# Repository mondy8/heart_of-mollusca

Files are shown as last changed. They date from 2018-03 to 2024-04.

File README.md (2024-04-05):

# Heart of Mollusca

+ [Heart of Mollusca 紹介動画](https://vimeo.com/240353748)
+ [ADAA アジアデジタルアートアワード 学生インタラクティブアート部門 優秀賞](https://adaa.jp/ja/winners/winners2017.html)
+ [北九州デジタルクリエイターコンテスト2018 入選](https://kdcc.info/archive/2018.html)
+ [ADADA2016 Art paper](https://github.com/ImaokaHiroaki/heart_of-mollusca/blob/master/paper/art_paper.pdf)

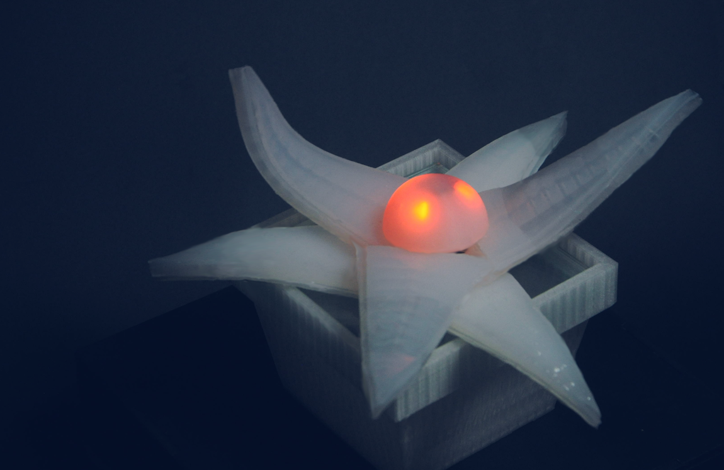
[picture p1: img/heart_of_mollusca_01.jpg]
写真1

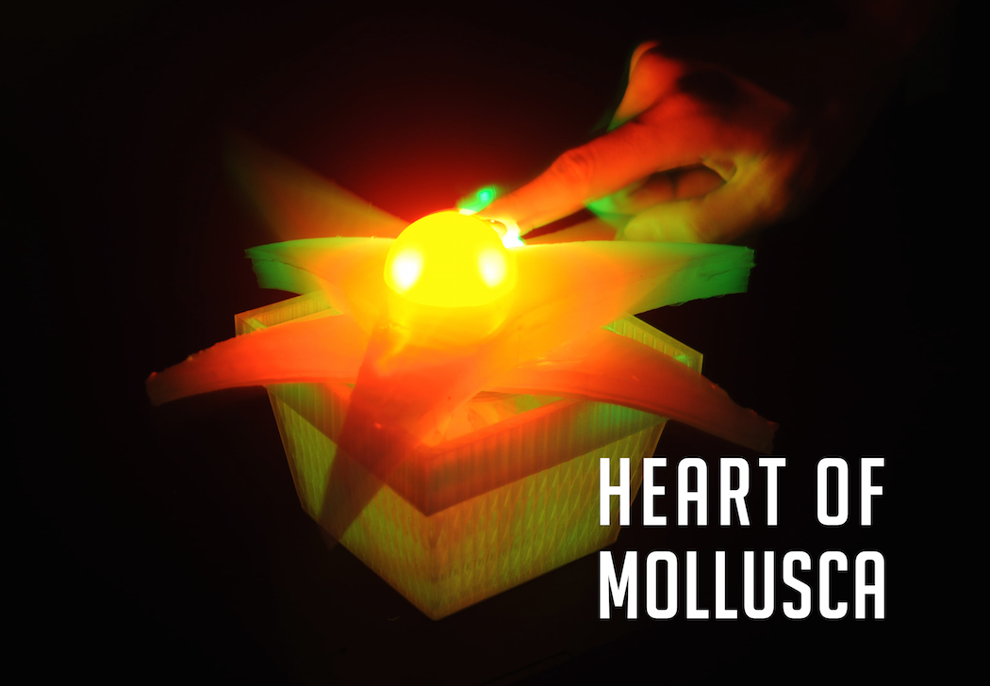
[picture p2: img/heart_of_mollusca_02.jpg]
写真2

 
 従来のロボットのイメージには「機械的」というキーワードが常に存在していた。ロボットは重厚であり、硬く、冷たいといったイメージである。それゆえに、ロボットには心がない、人間とロボットがコミュニケーションをとることはできない、といった意見が現状では多く見られる。昨今登場したソフトロボティクスという分野は、柔らかいロボットを研究する分野である。ソフトロボティクスを専攻している研究者たちは、「柔らかさ」をテーマにしたロボットを制作することで、何か今までになかったロボットの新しい可能性を探求している。本作品では、従来のロボットのイメージとは異なる有機的な表現を取り入れたロボットを制作することで、今までになかった新たなロボットとのコミュニケーションを実現したいと考えている。

 「Heart of Mollusca」は、人間の心拍とともに動くソフトロボットである。このロボットは、何もしていない状態だと動かず、人の心拍を検知した時、その人の心拍に合わせた動きを始める。鑑賞者はまず、作品の触手の部分にあるパルスセンサーを触る。すると「Heart of Mollusca」の中心部はゆっくりと赤く光りはじめる。そのあと、心拍と共に触手の部分が呼吸をするように膨張・収縮を繰り返す。人差し指で触手を触っているため、心拍にあわせた触手の膨張を感じることができる。「Heart of Mollusca」は、シリコンを使って中から空気を入れることによって動かしている。このシリコンによる柔らかさを用いた軟体動物のような動きは、鑑賞者に独特な感覚をもたらす。
 
 「Heart of Mollusca」を体験した鑑賞者たちは、今まで持っていた従来のロボットとのイメージとの差から興味・関心を抱く人や、ロボットの外見から想像していなかった動きに驚き、生理的な嫌悪感を抱く人など、様々な反応の違いを見せた。有機的な表現を取り入れたことに関しては、心拍とロボットの動きを連動したことにより、ロボットから生命らしさを感じると答えた人が多かった。心拍との連動を取り入れたことに関しては、普段意識することのない自分の心拍を視覚と触覚により体験することで、興味深く感じた人を多く見受けることができた。「Heart of Mollusca」を体験した人たちからは従来のロボットとの触れ合いとは異なった反応が多く得ることができた。

## レシピ

1. シリコン
	+ Ecoflex [(サツク株式会社)](https://vimeo.com/240353748)
	+ DragonSkin [(サツク株式会社)](https://vimeo.com/240353748)
	+ SilPoxy [(サツク株式会社)](https://vimeo.com/240353748)
2. 電気系統
	+ Arduino UNO [(スイッチサイエンス)](https://www.switch-science.com/catalog/789/)
	+ ACアダプター *2 [(robotshop)](https://www.robotshop.com/jp/ja/sfe-power-supply-9vdc-650ma.html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)
	+ Arduino用USBケーブル[(robotshop)](https://www.robotshop.com/jp/ja/usb-cable-a-b-arduino.html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)
	+ ソレノイド電磁石バルブ [(amazon)](https://www.amazon.co.jp/uxcell-a14010700ux0271-uxcell-%E3%82%BD%E3%83%AC%E3%83%8E%E3%82%A4%E3%83%89%E9%9B%BB%E7%A3%81%E7%9F%B3%E5%BC%81-%E3%82%BD%E3%83%AC%E3%83%8E%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)
	+ 気圧センサー MIS-2500-015G [(秋月)](http://akizukidenshi.com/catalog/g/gP-07272/)
	+ 心拍センサー [(スイッチサイエンス)](https://www.switch-science.com/catalog/1135/)
	+ Mitsumi マイクロエアポンプ [(amazon)](https://www.amazon.co.jp/Mitsumi-R-14-%E3%83%9E%E3%82%A4%E3%82%AF%E3%83%AD%E3%82%A8%E3%82%A2%E3%83%9D%E3%83%B3%E3%83%97-200mA-%E3%83%9F%E3%83%8B%E3%83%9D%E3%83%B3%E3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)
	+ 2Aデュアルモーターコントローラー [(秋月)](http://akizukidenshi.com/catalog/g/gM-06680/)
3. 小物系
	+ シリコンチューブ 4mm x 6mm [(モノタロウ)](https://www.monotaro.com/g/00250063/)
	+ シリコンチューブコネクター (二方型・クロス型・T型) [(モノタロウ)](https://www.monotaro.com/p/8933/4497/)
	+ PP ディスクカップ [(モノタロウ)](https://www.monotaro.com/p/5843/8712/?t.q=%83%7E%83L%83V%83%93%83O%83J%83b%83v)
	+ 極薄ニトリルゴム手袋 [(モノタロウ)](https://www.monotaro.com/g/00277898/?t.q=%8E%E8%91%DC)
	+ アルミ丸パイプ [(モノタロウ)](https://www.monotaro.com/g/00280306/)
	+ テルモシリンジ [(モノタロウ)](https://www.monotaro.com/p/0292/1861/?t.q=%83V%83%8A%83%93%83W)
	+ 割り箸
	+ 計量器
	
4. 設備
	+ 真空チャンバー
	+ オーブン
	+ 3Dプリンター
	+ CNCミリングマシン（基板切削用）
	
## Arduino配線図

instruction 説明

## 3Dデータ素材

* 球体上部分
* 球体下部分
* Ecoflex用フタ部分
* Ecoflex用土台
* DragonSkin用土台

instruction 説明

## Eagle切削基板

instruction 説明

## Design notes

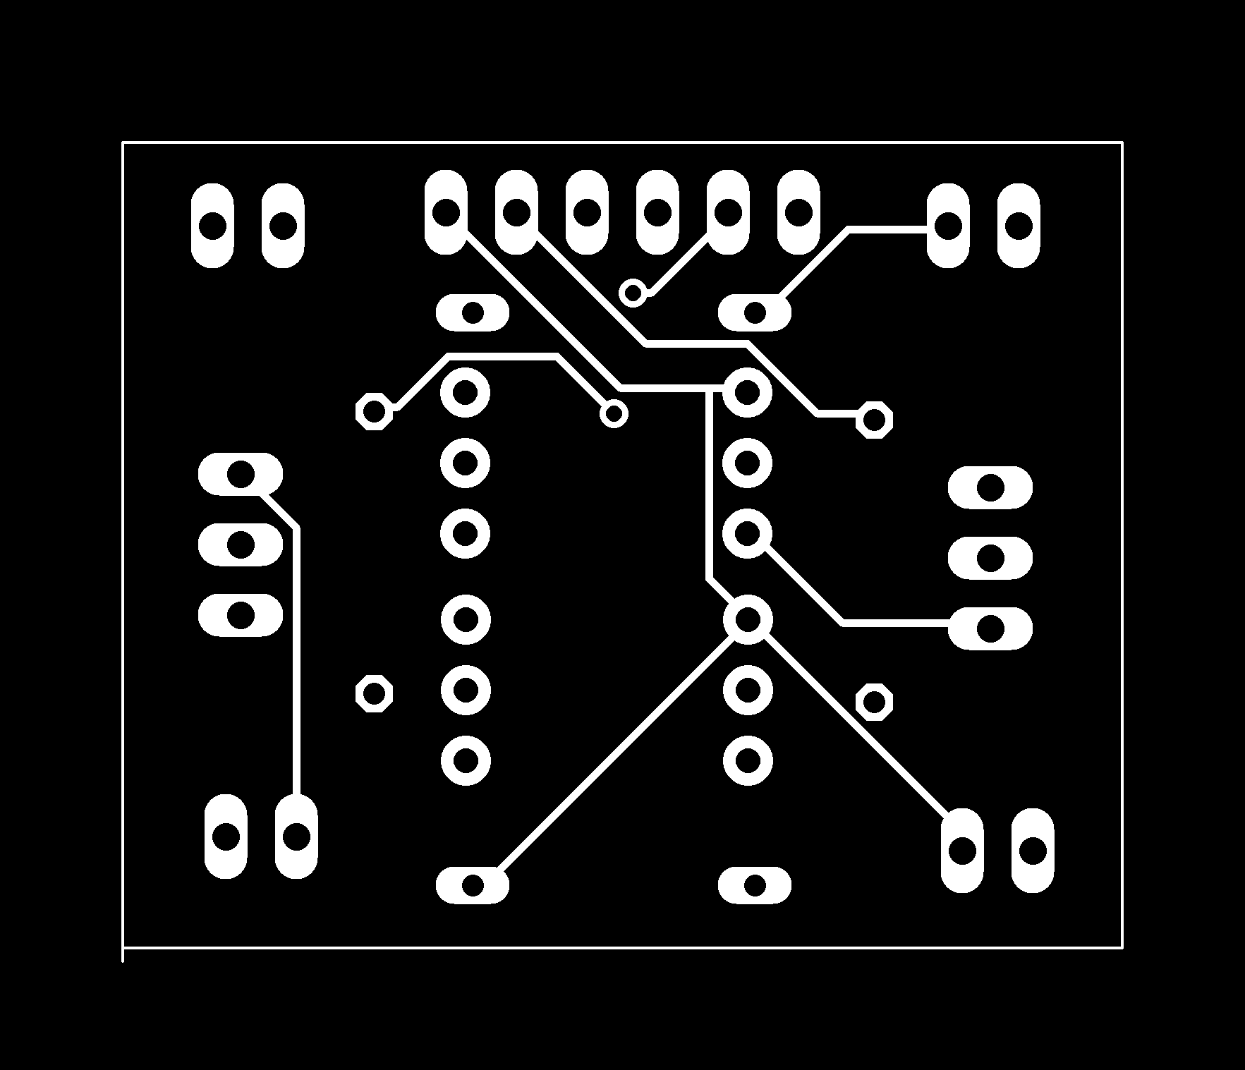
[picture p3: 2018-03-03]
Eagle/img/ura.png

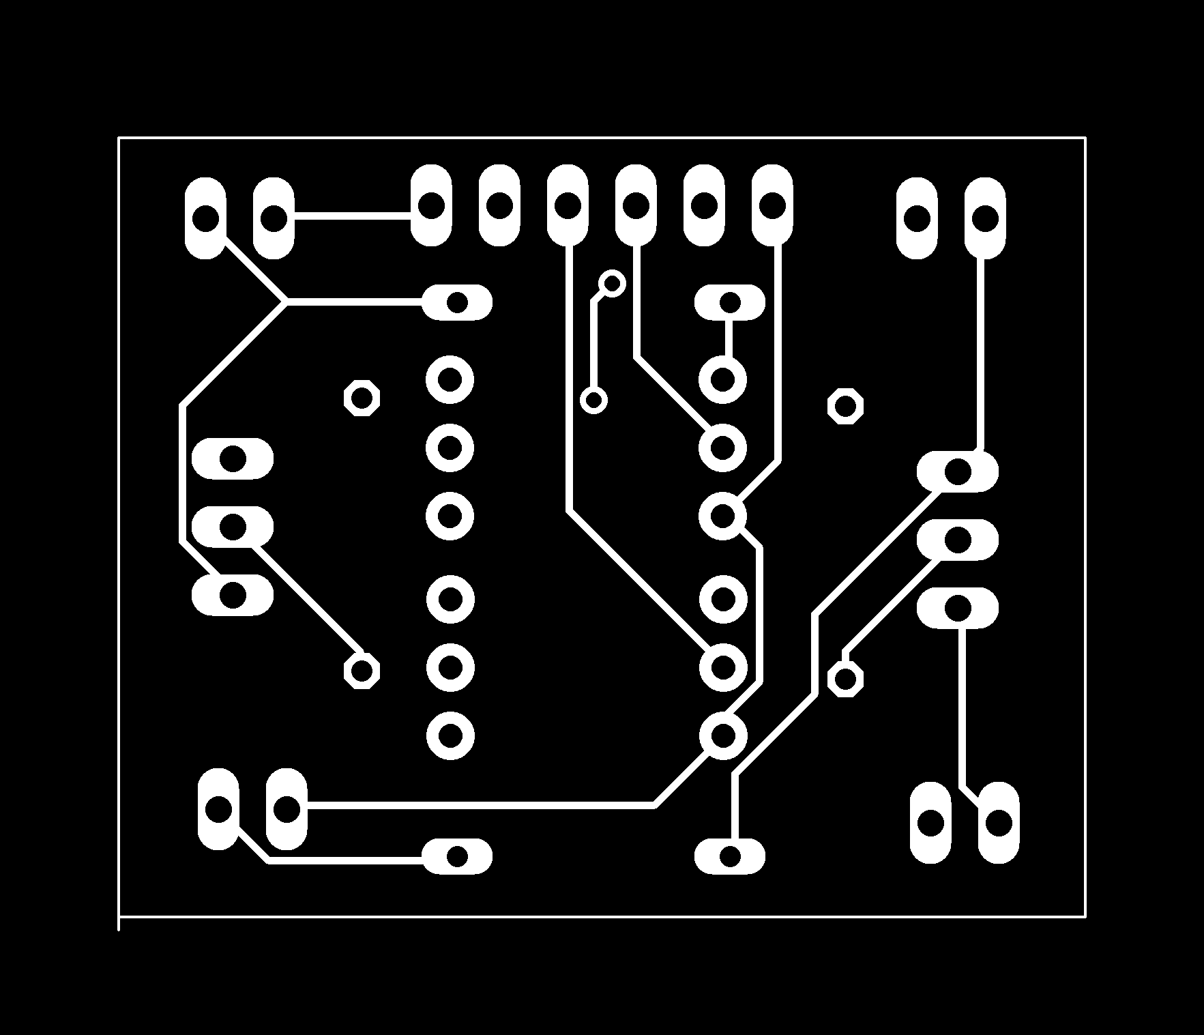
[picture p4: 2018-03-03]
Eagle/img/omote.png

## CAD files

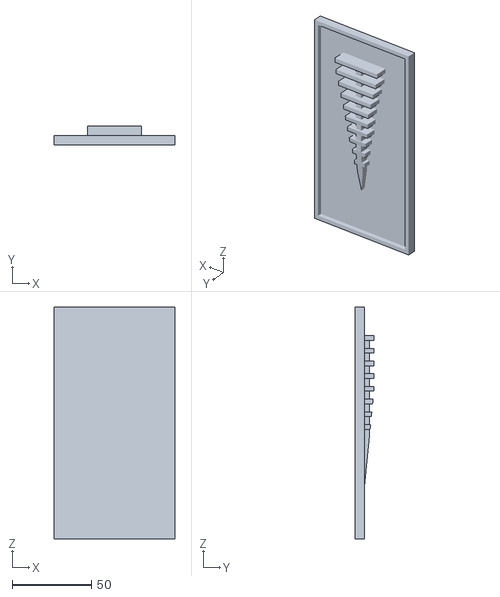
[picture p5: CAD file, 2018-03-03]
3D-data/mold_eco_shita.stl
76.0 x 12.0 x 146.0

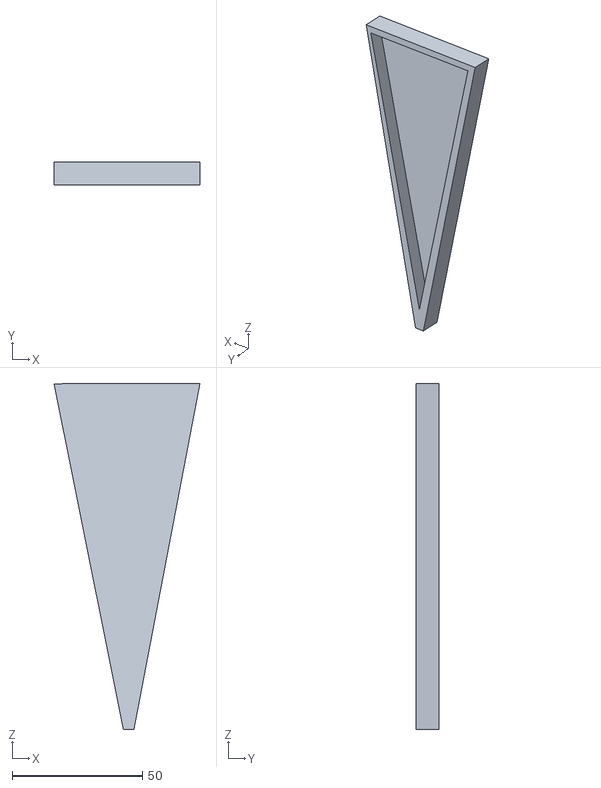
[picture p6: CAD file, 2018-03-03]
3D-data/mold_dragonskin.stl
56.1 x 9.00 x 133.0

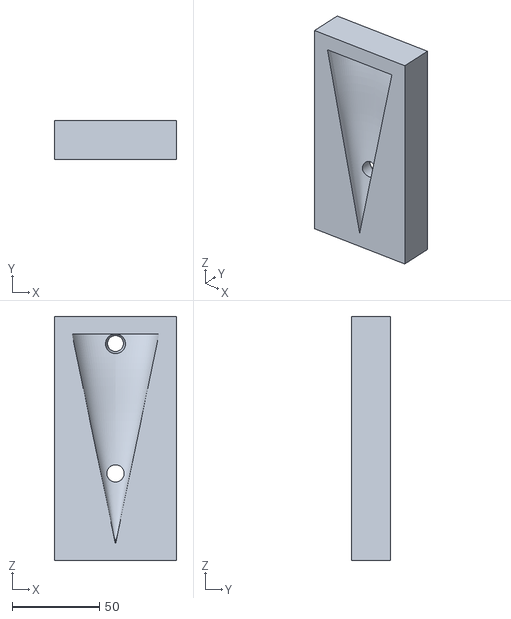
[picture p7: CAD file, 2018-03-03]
3D-data/mold_eco_futa.stl
70.0 x 22.5 x 140.0

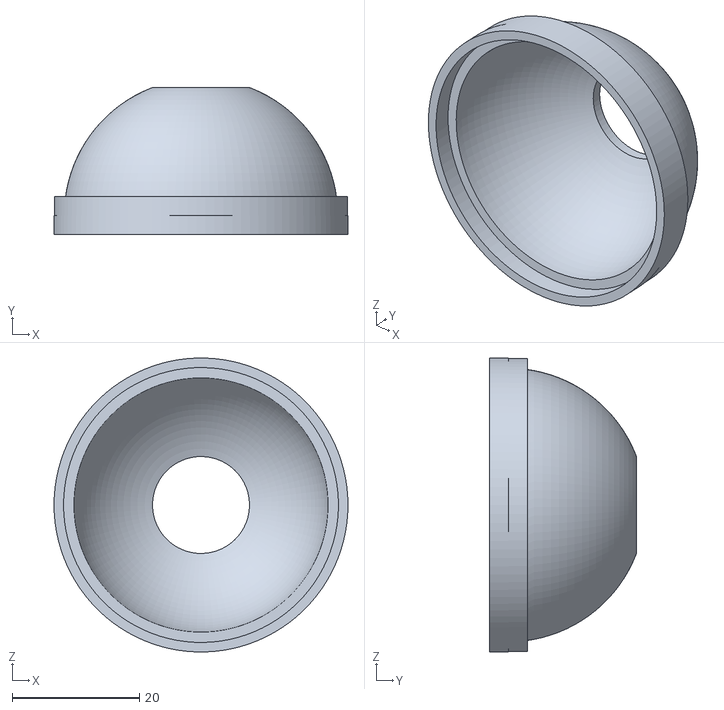
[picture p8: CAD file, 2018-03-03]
3D-data/circle_futa.stl
46.2 x 23.1 x 46.2

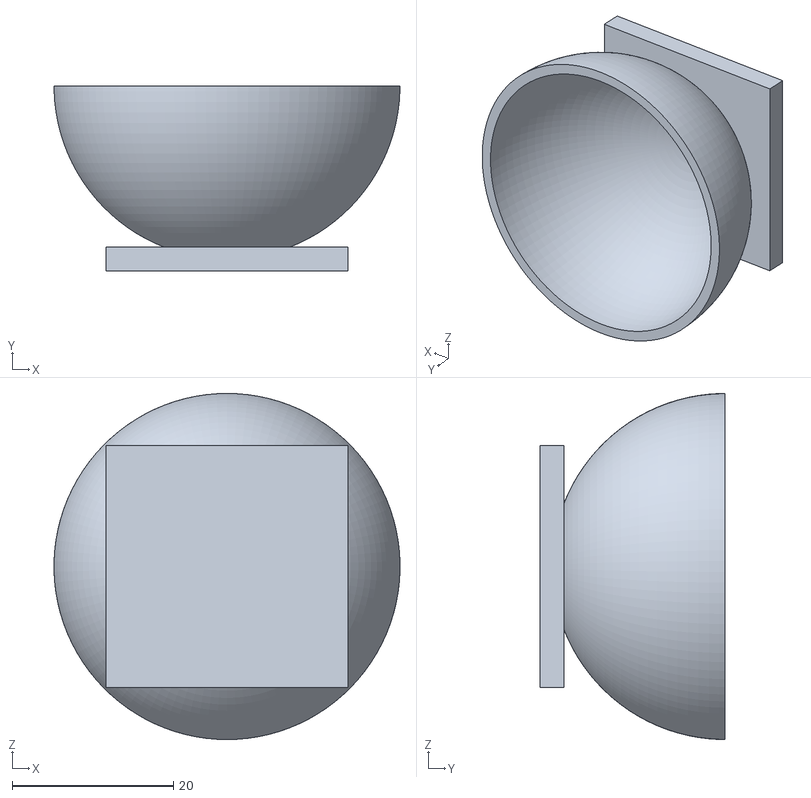
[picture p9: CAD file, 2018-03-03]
3D-data/circle_shita.stl
43.0 x 23.0 x 43.0

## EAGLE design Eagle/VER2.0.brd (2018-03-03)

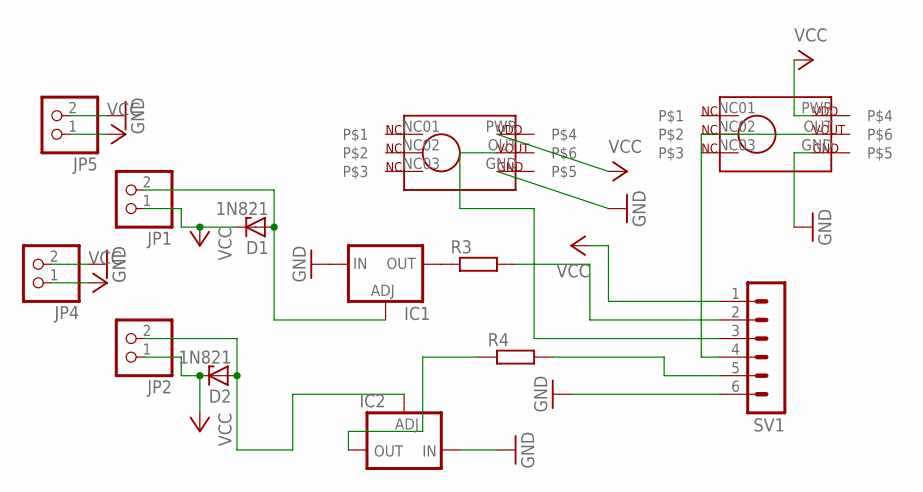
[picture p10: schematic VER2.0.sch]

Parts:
D1, D2: 1N821; DO35Z10
IC1, IC2: LM317TS; 317TS
JP1, JP2, JP4, JP5: PINHD-1X2; 1X02
R3, R4: R-EU_0207/10; 0207/10
SV1: MA06-1
U$1, U$2: MIS-2500

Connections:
GND: IC1.3 (IN), IC2.3 (IN), JP4.2, JP5.2, SV1.6, U$1.GND, U$2.GND
unnamed: R3.2, SV1.2
unnamed: SV1.3, U$1.OUT
unnamed: IC2.2 (OUT), R4.1
unnamed: D2.A, IC2.1 (ADJ), JP2.2
unnamed: IC1.2 (OUT), R3.1
unnamed: D1.A, IC1.1 (ADJ), JP1.2
unnamed: SV1.4, U$2.OUT
unnamed: R4.2, SV1.5
VCC: D1.C, D2.C, JP1.1, JP2.1, JP4.1, JP5.1, SV1.1, U$1.PWR, U$2.PWR

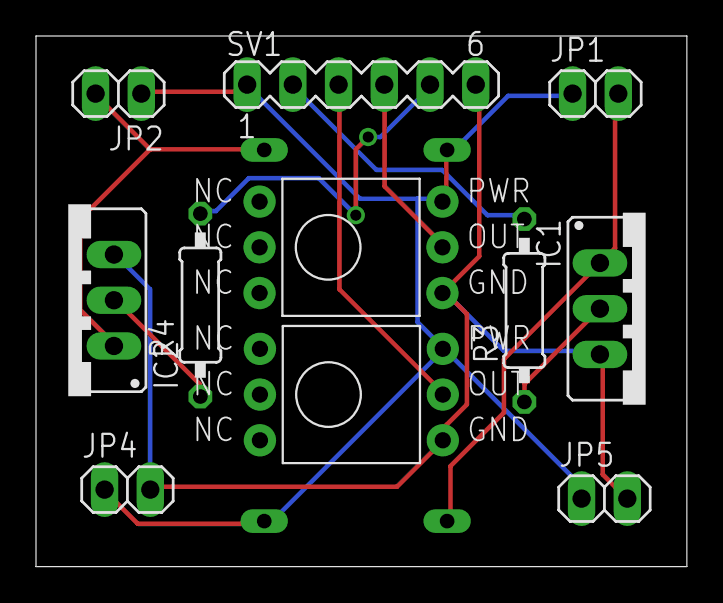
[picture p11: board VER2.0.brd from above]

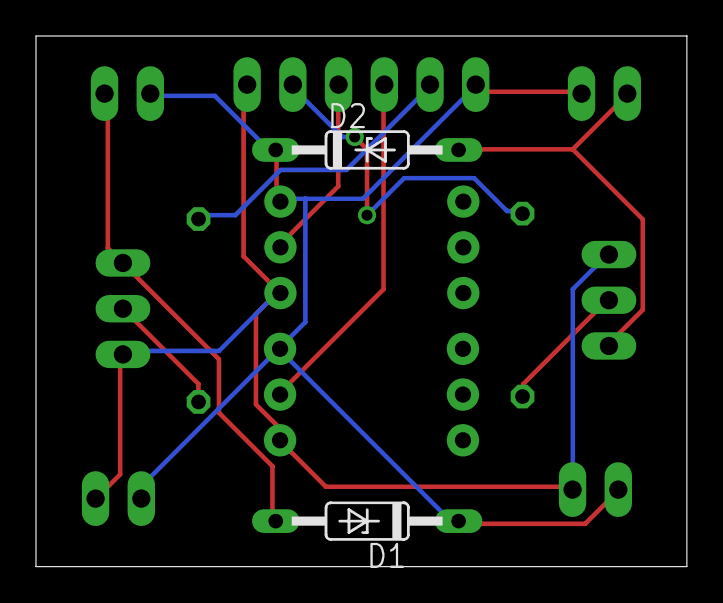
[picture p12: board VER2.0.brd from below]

Board: 2 copper layers, 36.2 x 29.5 mm, 13 parts (2 on the bottom side), 10 nets.

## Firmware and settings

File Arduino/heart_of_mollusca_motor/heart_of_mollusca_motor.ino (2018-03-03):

#include <Wire.h>

//Wire settings
#define deviceId 100
byte recievedValue = 0;
int deadCount = 0;

//---------pulse sensor------------
//unsigned long delayTime;
//  Variables
#define fadePin 6                  // pin to do fancy classy fading blink at each beat
int fadeRate = 0;                 // used to fade LED on with PWM on fadePin

//---------pump motor valve ------------
#define pumpEnable01  9 //analogWriteなのでPWM
#define pumpEnable02  10 //analogWriteなのでPWM
#define pumpMotor01   8 
#define pumpMotor02   7
#define valve1        11  //pump01      "HIGH == open" "LOW == closed"
#define valve2        12  //pump02

//ポンプの動作状態
typedef enum{
  PS_AIR_IN,
  PS_AIR_OUT
}PumpState;
PumpState pumpState;

//typedef enum{
//  VALVE_CLOSE,
//  VALVE_OPEN,
//  DEAD
//}PumpState02;
//PumpState02 pumpState02;

void setup(){
  pinMode(fadePin,OUTPUT);          // pin that will fade to your heartbeat!
  Serial.begin(9600);             // we agree to talk fast!

  //-----Wire setings---------
  Wire.begin(deviceId);
  Wire.onReceive(ReceivePulse);

  //-----↓pump setting---------
  pinMode(pumpEnable01,OUTPUT);
  pinMode(pumpMotor01,OUTPUT);
  pinMode(pumpEnable02,OUTPUT);
  pinMode(pumpMotor02,OUTPUT);
  
  pinMode(valve1,OUTPUT);
  pinMode(valve2,OUTPUT);
  
  pumpState = PS_AIR_OUT;
}

//  Where the Magic Happens
void loop(){
  check ();
  motion();
  delay(30);
}

void check () {

    if(recievedValue == 0) {
       pumpState = PS_AIR_OUT;
       deadCount++;
    }
    if(recievedValue == 1) {
    }

    if(recievedValue == 2) {//心拍感じたとき
      fadeRate = 255;
      if(pumpState == PS_AIR_OUT){
       pumpState = PS_AIR_IN;
      }else{
       pumpState = PS_AIR_OUT;
      }
      delay(100);
    }

    if(recievedValue == 3) {
      fadeRate = 255;
    }

/*   脈打つタイプ
    if(recievedValue == 0) {
       pumpState02 = DEAD;
    }
    if(recievedValue == 1) {
      analogWrite(fadePin, 100);
      pumpState02 = VALVE_OPEN;
    }

    if(recievedValue == 2) {//心拍感じたとき
      fadeRate = 255;
      pumpState02 = VALVE_CLOSE;
    }
    */

    if(deadCount>120){
      fadeRate = 255;
      deadCount = 0;
    }
}

void motion() {
  
  
  //pump motion
  pumpSafety();
  
  switch (pumpState) {
    
    case PS_AIR_IN:
      digitalWrite(pumpMotor01, HIGH);
      analogWrite(pumpEnable01, 140); //Max 255
      digitalWrite(valve1,LOW);
      
      digitalWrite(pumpMotor02, HIGH);
      analogWrite(pumpEnable02, 170); //Max 255
      digitalWrite(valve2,LOW);
    break;
    
    default:
    case PS_AIR_OUT:
      digitalWrite(pumpMotor01, LOW);
      analogWrite(pumpEnable01, 0); //Max 255
      digitalWrite(valve1,HIGH);
      digitalWrite(pumpMotor02, LOW);
      analogWrite(pumpEnable02, 0); //Max 255
      digitalWrite(valve2,HIGH);
    break;
  }

    fadeRate -= 15;                         //  set LED fade value
    fadeRate = constrain(fadeRate,0,255);   //  keep LED fade value from going into negative numbers!
    analogWrite(fadePin,fadeRate);          //  fade LED
}

//ポンプの安全を守る
void pumpSafety () {
  int pressure01 = analogRead(A1);
  int pressure02 = analogRead(A2);
  //Serial.println((String)"pressure: " + pressure01 + ", " + pressure02);
  
  if(pressure01 > 270 || pressure02 > 240 ) {
      fadeRate = 255;
      digitalWrite(valve1,HIGH);
      digitalWrite(pumpMotor01, LOW);
      analogWrite(pumpEnable01, 0);
      
      digitalWrite(valve2,HIGH);
      digitalWrite(pumpMotor02, LOW);
      analogWrite(pumpEnable02, 0);
      
      delay(1000); 
    }
}

void ReceivePulse (int numBytes) {
  byte value = Wire.read();
  Serial.println((String)"Receive " + value + (String)" : PumpState " + pumpState );
  recievedValue = value;
}

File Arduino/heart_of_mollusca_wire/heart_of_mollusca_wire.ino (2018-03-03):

#include<Wire.h>
#include <CapacitiveSensor.h>

#define USE_ARDUINO_INTERRUPTS true    // Set-up low-level interrupts for most acurate BPM math.
#include <PulseSensorPlayground.h>     // Includes the PulseSensorPlayground Library.   


#define deviceID 100

//  Variables
const int PulseWire = 0;       // PulseSensor PURPLE WIRE connected to ANALOG PIN 0
int Threshold = 550;           // Determine which Signal to "count as a beat" and which to ignore.
                               // Use the "Gettting Started Project" to fine-tune Threshold Value beyond default setting.
                               // Otherwise leave the default "550" value. 
PulseSensorPlayground pulseSensor;  // Creates an instance of the PulseSensorPlayground object called "pulseSensor"

CapacitiveSensor capSensor = CapacitiveSensor (5,4);
int threshold = 200; //capacity of touch sensor

void setup() {   

  Serial.begin(9600);          // For Serial Monitor

  Wire.begin();

  // Configure the PulseSensor object, by assigning our variables to it. 
  pulseSensor.analogInput(PulseWire);   
  pulseSensor.setThreshold(Threshold);   

  // Double-check the "pulseSensor" object was created and "began" seeing a signal. 
   if (pulseSensor.begin()) {
    Serial.println("We created a pulseSensor Object !");  //This prints one time at Arduino power-up,  or on Arduino reset.  
  }
}

void loop () {
  checkPulse();
}

void checkPulse() {
  //送信する値
  byte value = 0;
  
  // Calls function on our pulseSensor object that returns BPM as an "int".
  // "myBPM" hold this BPM value now. 
  int myBPM = pulseSensor.getBeatsPerMinute();  

  long sensorValue = capSensor.capacitiveSensor(30);
  
  Serial.println((String)"touch:" + sensorValue + " bpm: " + myBPM);
  if (sensorValue > threshold && pulseSensor.sawStartOfBeat()) {
    value = 2;
    delay(10);
  }else if(sensorValue > threshold){
    value = 1; //BPMは無いけど、タッチされている場合
  }
  if (sensorValue == -2) value = 3;

  SendPulse(value);

  delay(50);                    // considered best practice in a simple sketch.

}

void SendPulse (byte value) {
  Wire.beginTransmission(deviceID);
  Wire.write(value);
  Wire.endTransmission();
}

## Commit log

2018-03-03 3Ddata更新、eagle説明更新
    [mold_dragonskin.stl, mold_eco_futa.stl, mold_eco_shita.stl]
2018-03-03 3D説明更新
2018-03-03 説明更新
2024-04-05 Art Paper追加
2024-04-05 リンク修正
